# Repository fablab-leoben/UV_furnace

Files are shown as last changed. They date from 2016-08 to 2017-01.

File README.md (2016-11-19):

# UV furnace

## Table of contents

### 1. [Introduction](https://github.com/fablab-leoben/UV_furnace/blob/master/README.md#1-introduction-1 "Introduction")
### 2. [Bill of materials](https://github.com/fablab-leoben/UV_furnace/blob/master/README.md#2-bill-of-materials-1 "Bill of Materials")
### 3. [Required tools](https://github.com/fablab-leoben/UV_furnace/blob/master/README.md#3-required-tools-1 "Required tools")
### 4. [CAD design](https://github.com/fablab-leoben/UV_furnace/blob/master/README.md#4-cad-design-1 "CAD design")
### 5. [Circuit](https://github.com/fablab-leoben/UV_furnace/blob/master/README.md#5-circuit-1 "Circuit")
### 6. [Human Machine Interface (HMI)](https://github.com/fablab-leoben/UV_furnace/blob/master/README.md#6-human-machine-interface-hmi-1 "Human Machine Interface (HMI)")
#### 6.1 [HMI Screenshots](https://github.com/fablab-leoben/UV_furnace/blob/master/README.md#61-hmi-screenshots-1 "HMI Screenshots")
#### 6.2 [Flashing the display](https://github.com/fablab-leoben/UV_furnace/blob/master/README.md#62-flashing-the-display-1 "Flashing the display")
### 7. [Arduino MEGA 2560](https://github.com/fablab-leoben/UV_furnace/blob/master/README.md#7-arduino-mega-2560-1 "Arduino MEGA 2560")
#### 7.1 [Arduino IDE](https://github.com/fablab-leoben/UV_furnace/blob/master/README.md#71-arduino-ide-1 "Arduino IDE")
#### 7.2 [Installing the libraries](https://github.com/fablab-leoben/UV_furnace/blob/master/README.md#72-installing-the-libraries-1 "Installing the libraries")
#### 7.3 [Flashing the code](https://github.com/fablab-leoben/UV_furnace/blob/master/README.md#73-flashing-the-code-1 "Flashing the code")
### 8. [App](https://github.com/fablab-leoben/UV_furnace/blob/master/README.md#8-app-1 "App")
#### 8.1 [Screenshot](https://github.com/fablab-leoben/UV_furnace/blob/master/README.md#81-screenshot-1 "Screenshot")
#### 8.2 [Measuring the temperature](https://github.com/fablab-leoben/UV_furnace/blob/master/README.md#82-measuring-the-temperature-1 "Measuring the temperature")
#### 8.3 [Time and alarms](https://github.com/fablab-leoben/UV_furnace/blob/master/README.md#83-time-and-alarms-1 "Time and alarms")
#### 8.4 [Relay](https://github.com/fablab-leoben/UV_furnace/blob/master/README.md#84-relay-1 "Relay")
#### 8.5 [LEDs](https://github.com/fablab-leoben/UV_furnace/blob/master/README.md#85-leds-1 "LEDs")
#### 8.6 [Persistant data](https://github.com/fablab-leoben/UV_furnace/blob/master/README.md#86-persistant-data-1 "Persistant data")
### 9. [Logging and visualization](https://github.com/fablab-leoben/UV_furnace/blob/master/README.md#9-logging-and-visualization-1 "Logging and visualization")
#### 9.1 [Requirements](https://github.com/fablab-leoben/UV_furnace/blob/master/README.md#91-requirements-1 "Requirements")
#### 9.2 [Install InfluxDB & Grafana](https://github.com/fablab-leoben/UV_furnace/blob/master/README.md#92-install-influxdb--grafana-1 "Install InfluxDB & Grafana")
#### 9.3 [Configuration](https://github.com/fablab-leoben/UV_furnace/blob/master/README.md#93-configuration-1 "Configuration")
##### 9.3.1 [InfluxDB](https://github.com/fablab-leoben/UV_furnace/blob/master/README.md#931-influxdb "InfluxDB")
##### 9.3.2 [Grafana](https://github.com/fablab-leoben/UV_furnace/blob/master/README.md#932-grafana "Grafana")
#### 9.4 [Demonstration](https://github.com/fablab-leoben/UV_furnace/blob/master/README.md#94-demonstration-1 "Demonstration")
### 10. [App](https://github.com/fablab-leoben/UV_furnace/blob/master/README.md#10-app-1 "App")
#### 10.1 [Features](https://github.com/fablab-leoben/UV_furnace/blob/master/README.md#101-features "Features")
#### 10.2 [App installation](https://github.com/fablab-leoben/UV_furnace/blob/master/README.md#101-app-installation-1 "App installation")
### 11. [To Do](https://github.com/fablab-leoben/UV_furnace/blob/master/README.md#11-to-do-1 "To Do")

### 1. Introduction

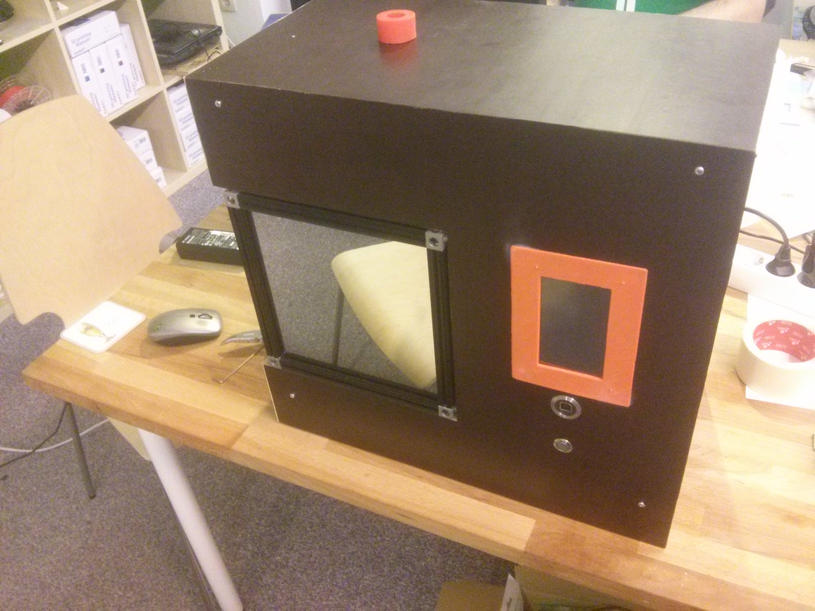
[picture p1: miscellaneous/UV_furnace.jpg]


3D printing is an advanced and environmentally friendly manufacturing method. It is a rapidly growing market both private and commercial. It is not just that they help you to act out your creativity or building prototypes, you are also able to repair things where you will not get any spare parts. They are also used in the medical and aerospace industry!
[SLA](https://en.wikipedia.org/wiki/Selective_laser_sintering) and [DLP](https://en.wikipedia.org/wiki/Digital_Light_Processing) printer are growing increasingly from an expensive niche to a consumer product.
The [Fablab in Leoben](http://www.fablab-leoben.at/) has a commercial [Form One](http://formlabs.com/de/produkte/3d-printers/form-1-plus/) and a **self built** [DLP printer](https://github.com/fablab-leoben/Fab-dlp). These printers usually need some form of post curing with additional UV light and heat to strengthen the printed parts. This would help to open more application areas for SLA/DLP resin printer to help saving ressources and our environment.
During our DLP printer build and because of our experience with the Form One we tried several methods to post-cure the parts after printing. The perfect solution was not found in our experiments so we decided to build our own UV furnace.

Broken parts printed with a Formlabs Form One SLA printer:
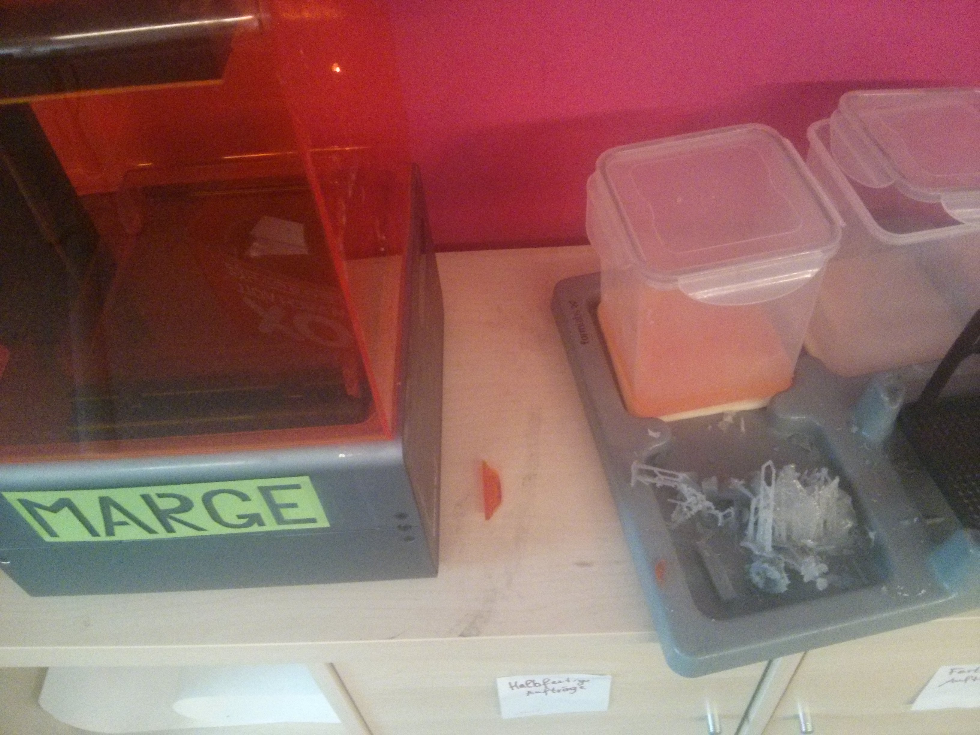
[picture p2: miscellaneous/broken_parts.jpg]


DLP Printer of the Fablab Leoben:
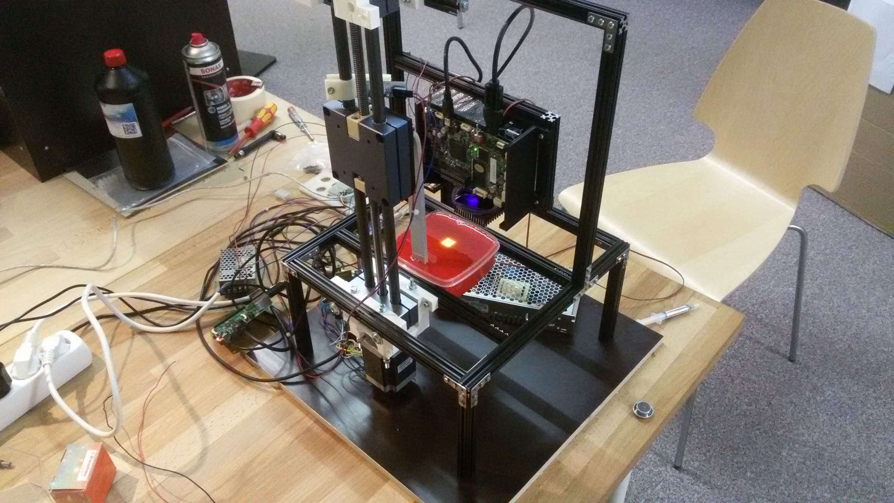
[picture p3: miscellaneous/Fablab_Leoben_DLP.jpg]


Successfull print of [Aria the Dragon](https://www.youmagine.com/designs/aria-the-dragon)
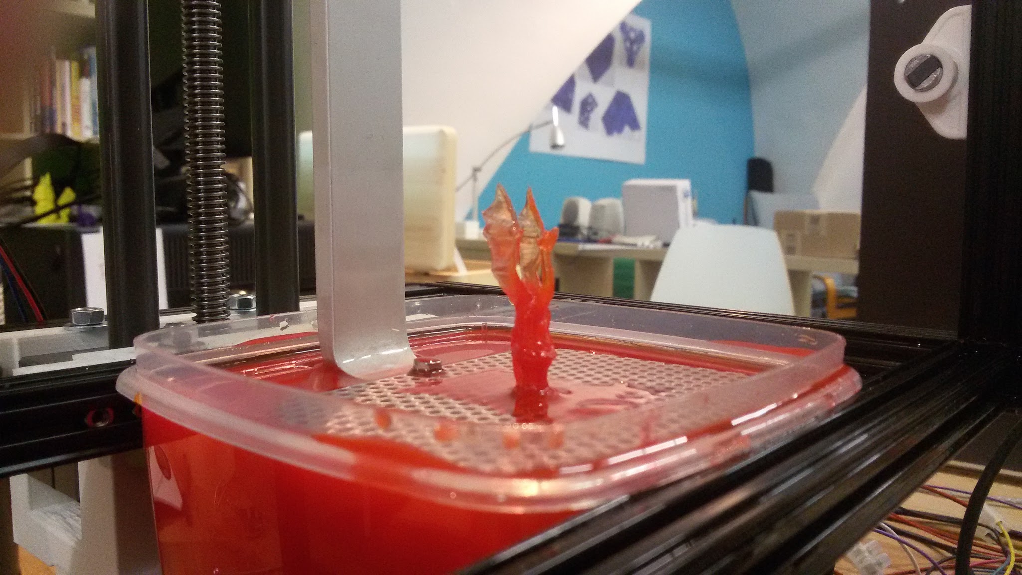
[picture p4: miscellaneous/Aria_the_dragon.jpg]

It looks great but you have to be very careful because the resin is not fully cured. So it is an ideal candidate for the UV furnace.

During the last few months I have designed and built this furnace. It is already working but still under heavy development to include new features and fix small bugs. 

UV furnace video (http://www.youtube.com/watch?v=noe39QOHljc)

### 2. Bill of materials

| Pos. | Pieces | Unit |  Name | comment |
|---|---|---|---|---|
| 1  | 1 |  []  | Arduino Mega 2560 R3 | |
| 2  | 1 |  []  | Arduino Ethernet Shield 2 | |
| 3  | 1 |  []  | Adafruit Thermoelement-Verstärker MAX31855 breakout board - v2.0 | |
| 4  | 1 |  []  | Thermocouple Type-K Glass Braid Insulated - K | |
| 5  | 1 |  []  | Adafruit Magnetic contact switch (door sensor) | Normally open reed switch |
| 6  | 2 |  []  | Kingston 8 GB Micro-SDHC Class10 Speicherkarte | any Micro-SD card is ok |
| 7  | 1 |  []  | Adafruit ChronoDot - Ultra-precise Real Time Clock - v2.1 | |
| 8  | 1 |  []  | Adafruit VEML6070 UV Index Sensor Breakout | optional |
| 9  | 1 |  []  | Adafruit Rugged Metal Pushbutton with LED Ring | |
|  10  | 1 |  []  | Male DC Power adapter - 2.1mm plug to screw terminal block | |
|  11  | 1 |  []  | 5V 1 channel relay shield for Arduino | |
|  12  | 1 |  []  | MEAN WELL RS-25-12 | |
|  13  | 1 |  []  | MEAN WELL LDD-350HW | |
|  14  | 2 |  []  | MEAN WELL LDD-500HW | |
|  15  | 3 |  []  | FISCHER ELEKTRONIK SK57750SA | |
|  16  | 1 |  []  | MEAN WELL PM-10-5 | |
|  17  | 1 |  []  | 240 V 50 W heater mat | |
|  18  | 1 |  []  | Nichia SMD LED UV NCSU275 365 nm | on a 10 x 10 mm pcb |
|  19  | 1 |  []  | Nichia SMD LED UV NCSU275 400 nm | on a 10 x 10 mm pcb |
|  20  | 1 |  []  | NIKKISIO 300 nm LED from EQ Photonics GmbH | ~ 260 €/piece (optional)  |
|  21  | 1 |  []  | Arctic Silver Wärmeleitkleber (2x 3.5g) | |
|  22  | 1 |  []  | fused quarz glass plate 200 x 200 x 2 mm | |
|  23  | 1 |  []  | Aluminium plate 200x200x3 | |
|  24  | 1 |  []  | Geocel Plumba Flue Silikondichtmasse, bis+315°C, Kartusche, 310ml | optional |
|  25  | 1 |  []  | IEC-Steckverbinder C14, Tafelmontage, gerade 10A 250 V ac | |
|  26  |  24 |  []  | Openbeam Corner Cubes | |
|  27  |  10 | [m]  | Openbeam beam | |
|  28  |  36 |  []  | Makerbeam Corner brackets | |
|  29  | 4 |  []  | Feet for Openbeam | |
|  30  | 1 |  []  | Thread forming screw set for OpenBeam | |
|  31  |  24 |  []  | MakerBeam Right angle brackets | |
|  32  |  12 |  []  | MakerBeam T brackets | |
|  33  | 2 |  []  | MakerBeam Button Head Socket Bolt | |
|  34  | 1 |  []  | MakerBeam M3 regular nuts | |
|  35  | 1 |  []  | MakerBeam M3 knurled nuts | |
|  36  | 1 |  []  | MakerBeam M3 cap nuts | |
|  37  | 1 |  []  | USB 2.0 Anschlusskabel USB 2.0 Stecker A - USB 2.0 Stecker B 1.80 m | |
|  38  | 1 |  []  | USB 2.0 Anschlusskabel USB 2.0 Stecker A - USB 2.0 Stecker B 0.50 m | |
|  39  | 1 |  []  | USB-Einbaubuchse vorne USB-Buchse Typ B · hinten USB-Buchse Typ A | optional |
|  40  | 1 |  []  | RJ45-Einbaubuchse Buchse, Einbau, Stecker, gerade Pole: 8P8C RRJVA_RJ45 | optional |
|  41  | 1 |  []  | Netzkabel, C13 auf Stecker mit Schutzleiterkontakt, 2,5m, 16 A, 250 V | |
|  42  | 5 |  []  | mirror flagstone 200 x 200 mm | metallised with Aluminium |
|  43  | 1 |  []  | Nextion 4,3" Touch Display NX4827T043 | |
|  44  | 1 |  []  | [Arduino Mega Screw Shield](http://www.crossroadsfencing.com/BobuinoRev17/)| optional |
|  45  | 2 |  []  | Fan SUNON PF80321B1-000U-S99 | optional |
|  46  | 3 |  []  | Resistor 4,7 kOhm | |
|  47  | 1 |  []  | shrink tubing | |
|  48  | 1 |  []  | bell wire or other wires in different colors | |
|  49  | 2 |  []  | small hinge from your local DIY market | |
|  50  | 1 | [m]  | three-pole electric cable 1,5 mm² | |
|  51  | 5 | [m]  | eight-pole bell wire | or other wires with different colors |
|  52  | 1 |  []  | Female/Male 'Extension' Jumper Wires - 40 x 6" | to wire the sensors |
|  53  | 1,5  | [m²] | plywood 12x1000x1500 mm | |

Estimated costs: **~1000 €**

It really depends on your manufacturing possibilities and the shops where you buy the components. Also be aware that we are using a 300 nm UV LED for **~260 €/piece**! Try to recycle parts when you have a low budget and drop expensive nice to have parts like the "USB-Einbaubuchse" and "RJ45-Einbaubuchse" which cost ~40 € each. So there is enough room to cut the costs down :)

### 3. Required tools

| Pos. | Tool | comment |
|---|---|---|
|  1 |  patience ;) | |
|  2 |  different Screwdrivers | |
|  3 |  different hex key drivers | |
|  4 |  3D Printer | |
|  5 |  soldering iron | |
|  6 |  drilling machine | |
|  7 |  different drills | |
|  8 |  hammer | |
|  9 |  small buzzsaw or Lasercutter | |
| 10 |  multimeter | |
| 11 |  jigsaw | |
| 12 |  lighter | for shrink tubing |
| 13 |  [Arduino IDE](https://www.arduino.cc/en/Main/Software)| |
| 14 |  [Nextion Editor](http://nextion.itead.cc/download.html)| to program the display |
| 15 |  Micro SD Card reader | |

### 4. CAD design

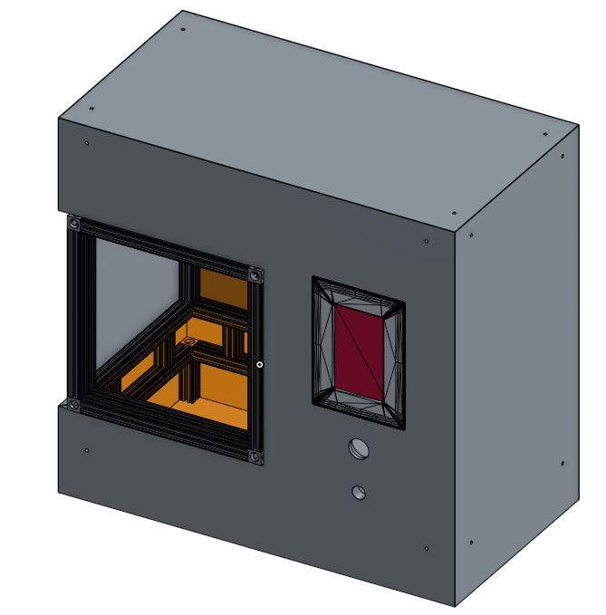
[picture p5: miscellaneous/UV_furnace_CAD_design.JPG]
UV furnace CAD design


The CAD Design was done with [Onshape](https://www.onshape.com/cad-pricing "Onshape"). It is free for Hobbyists, Makers.

You can find, modify and download the UV furnace design [here](https://cad.onshape.com/documents/65acaf65361afb5a9c027038/w/3b13638207107c108fe9135d/e/915e14169c92d702a1d86d80 "UV furnace design"). Feel free to modify the housing to fit your budget. 

### 5. Circuit

I have designed the circuit with [Fritzing](http://fritzing.org/download/). Download the free software to be able to modify the [circuit](https://github.com/fablab-leoben/UV_furnace/blob/master/circuit/UV_furnace_circuit.fzz).
Wire everything like on the picture below and check everything at least twice to make sure everything is wired correctly! Otherwise you can destroy your hardware and jeopardise your health.

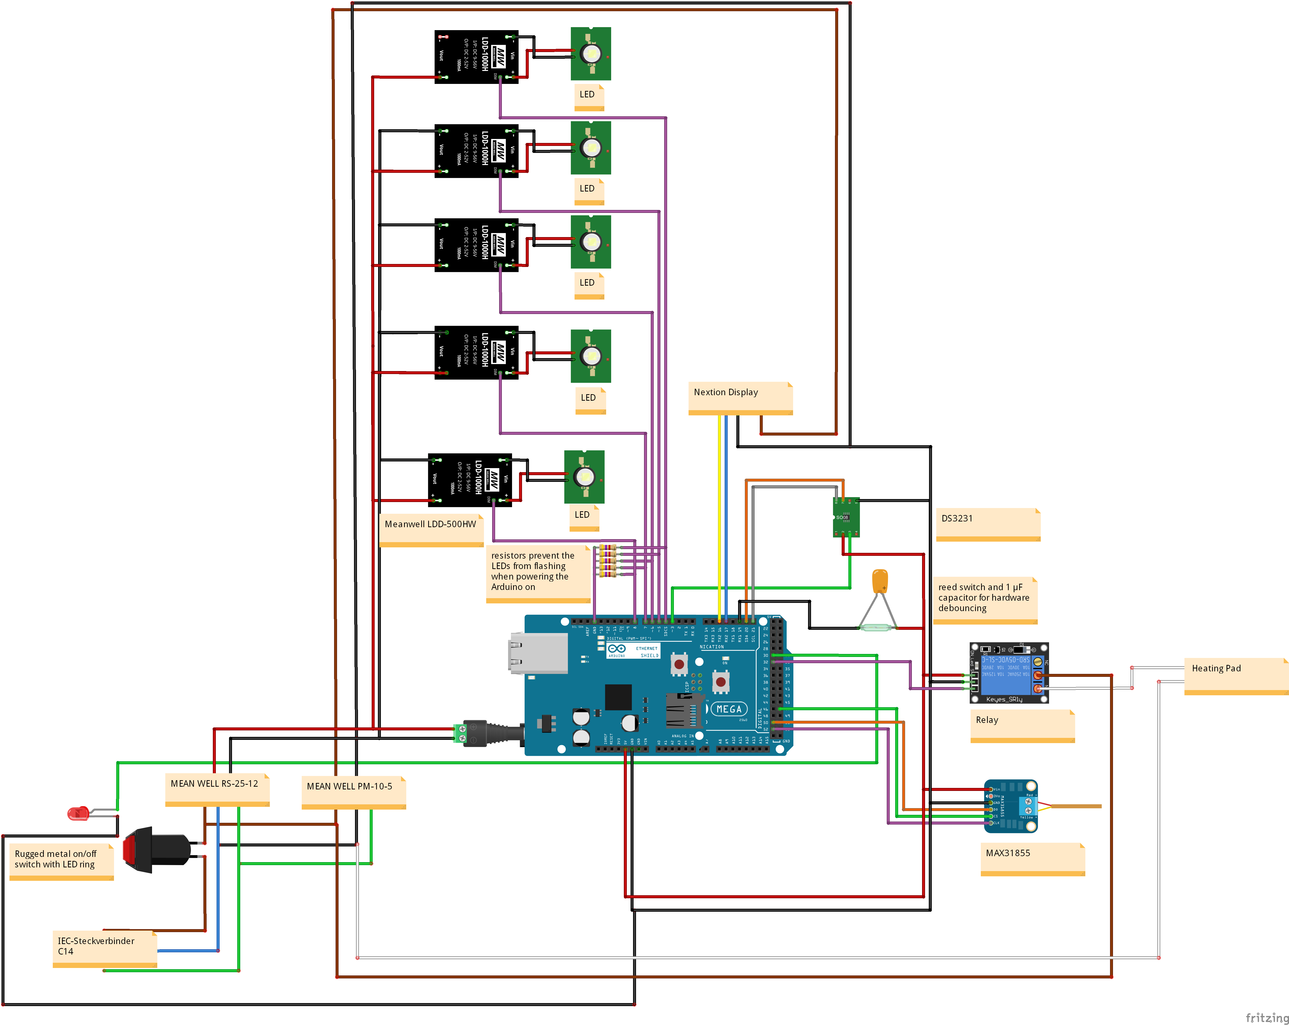
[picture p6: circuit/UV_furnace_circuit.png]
Circuit


Everything mounted in the furnace:
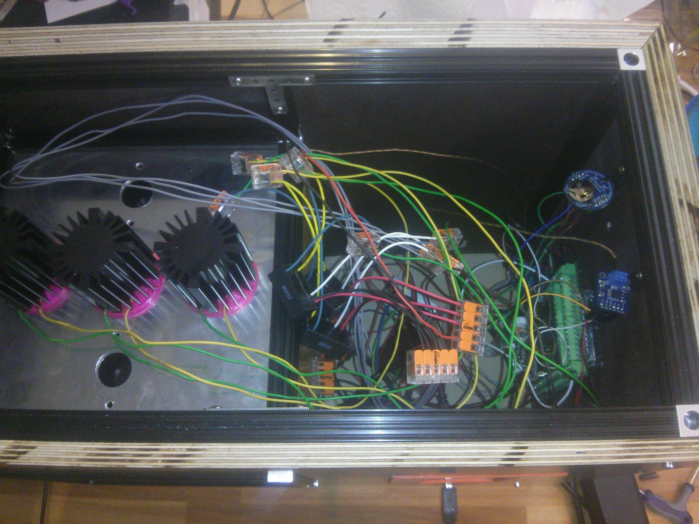
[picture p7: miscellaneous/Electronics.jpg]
Electronics


### 6. Human Machine Interface (HMI)

The HMI was designed with [Pencil](http://pencil.evolus.vn/), an open-source GUI prototyping tool that's available for ALL platforms. The interface is based on the [Material Design Guidelines](https://material.google.com/) from Google for better useability.

#### 6.1 HMI Screenshots

#### 6.2 Flashing the display

Save the [UV_furnace.tft](https://github.com/fablab-leoben/UV_furnace/blob/master/HMI/UV_furnace.tft) file on a micro SD card, insert it into the display and supply it with power. The flash process starts automatically. After that remove the micro SD card and repower the display.
If you would like to make changes to the interface just open [UV_furnace.HMI](https://github.com/fablab-leoben/UV_furnace/blob/master/HMI/UV_furnace.HMI) with the [Nextion editor](http://nextion.itead.cc/download.html).

### 7. Arduino Mega 2560

Because of the comprehensive features I had to use an Arduino Mega for this project.
Visit the [Getting started page](https://www.arduino.cc/en/Guide/HomePage) for more information on how to configure your board.

| Technical specification | |
|---|---|
| Microcontroller |	ATmega2560 |
| Operating Voltage |	5V |
| Input Voltage (recommended) |	7-12V |
| Input Voltage (limit) |	6-20V |
| Digital I/O Pins |	54 (of which 15 provide PWM output) |
| Analog Input Pins |	16 |
| DC Current per I/O Pin |	20 mA |
| DC Current for 3.3V Pin |	50 mA |
| Flash Memory |	256 KB of which 8 KB used by bootloader |
| SRAM	| 8 KB |
| EEPROM	| 4 KB |
| Clock Speed	| 16 MHz |
| Length |	101.52 mm |
| Width |	53.3 mm |
| Weight |	37 g |

#### 7.1 Arduino IDE

First of all download the [Arduino IDE](https://www.arduino.cc/en/Main/Software) and install it on your computer. It is available for Windows, Linux and Mac.

#### 7.2 Installing the libraries

Download the libraries.zip file and extract them into your Arduino libraries folder. The path for Windows computer is: 
>C:\Users\YourName\Documents\Arduino\libraries
If you do not have this folder do not hesitate to create it.

#### 7.3 Flashing the code

Open the Arduino IDE and connect your Arduino via USB to your computer. Under Tools/Board select Arduino Mega and choose the right serial port. 
Open the sketch UV_furnace.ino and click on the compile & flash button. The compiler now translates the code and writes it to your microcontroller.  

### 8. Noteworthy things

#### 8.1. Finite State Machine

My code uses a finite state machine (FSM) to make reading and understanding such a massive amount of code easier for everyone.

Definition of a Finite State Machine:
>A finite-state machine (FSM) or finite-state automaton (FSA, plural: automata), or simply a state machine, is a mathematical model of >computation used to design both computer programs and sequential logic circuits. It is conceived as an abstract machine that can be >in one of a finite number of states. The machine is in only one state at a time; the state it is in at any given time is called the >current state. It can change from one state to another when initiated by a triggering event or condition; this is called a >transition. A particular FSM is defined by a list of its states, and the triggering condition for each transition.

The FSM serves as a manager that organizes the states of the UV furnace.

#### 8.2 Measuring the temperature

The furnace uses a MAX31855 thermocouple amplifier to measure the temperature. You can use thermocouples also for temperatures over 1000 °C. Only the thermocouple is in the hot part of the furnace so you do not need to worry about damaging the amplifier.

#### 8.3 Time and alarms

During startup the furnace requests the current time via the Network Time Protocol (NTP) to set the time of the DS3231 realtime clock. The realtime clock is used to generate an alarm when the furnace has finished. The integrated temperature compensation is also used to check the temperature of the electronics and acts as a safety feature.

#### 8.4 Relay

The UV furnace has a high thermal mass, so the response time is slow. Therefore it is possible to use a cheap relay instead of a solid state relay to control the heating pad. In our case the response time will be 0,1 Hz or once every 10 seconds.
Take care of yourself when you wire the relay because there is mains voltage involved!

#### 8.5 LEDs

I use Meanwell LDD-500H LED driver to control the LEDs. They offer a wide input voltage range from 9 ~ 56 VDC and a high output voltage range from 2 ~ 52 VDC. Hence you are very flexible when you would like to use other LEDs with a different wavelength in your furnace. You only need to change the power supply if necessary. At the moment I am using three LEDs (red, green, white) in the visible light spectrum. Due to the fact that the furnace is under heavy development it is much more comfortable to add features, fix small bugs and test the workflow.
This shows the flexibility of the LED setup. Switching to UV LEDs is only a matter of minutes.

To be able to cure the 3D printed parts the UV light needs to light the curing area. We do not want to stress our light source with unnecessary heat when we cure our prints. Regular glass blocks most of the UV radiation. Because of that we use a quartz glass plate below the LEDs.

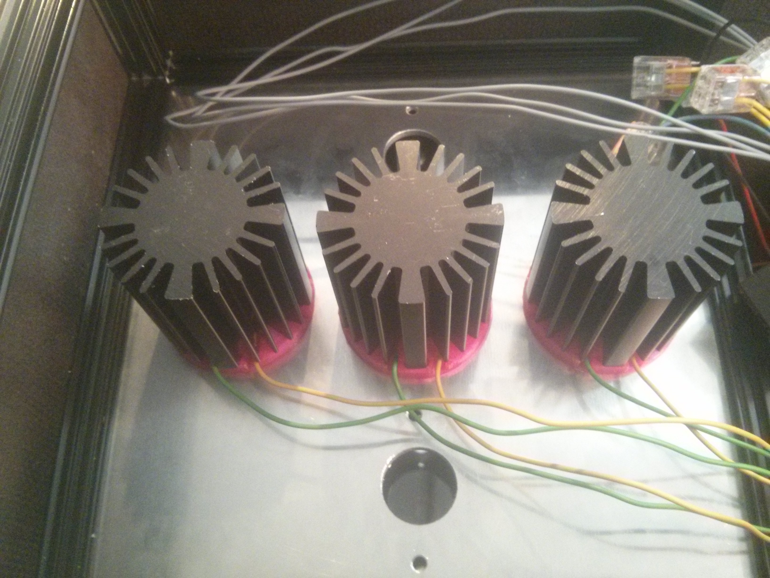
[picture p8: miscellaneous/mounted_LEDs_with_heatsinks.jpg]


#### 8.6 Persistant data

The tuning parameters for the PID controller are saved in the Arduino's EEPROM. Thus the UV furnace will remember the settings from the last time. EEPROM can only be written a finite number of times so we compare the contents before writing.

### 9. Logging and visualization

There are many use cases where data logging and visualization can be very useful so I have made an easy setup to achieve this functionality.

#### 9.1 Requirements
  * Computer running Ubuntu 
  * Install [Docker](docker.com)
  * create directory /media/nas/data/influxdb/
  * create directory /media/nas/data/grafana/
  
#### 9.2 Install InfluxDB & Grafana

Install command for InfluxDB
>sudo docker run -d -p 8083:8083 -p 8086:8086 --name influxdb -p 4444:4444/udp --expose 4444 -e UDP_DB="my_db" -v /media/nas/data/influxdb:/data --restart=unless-stopped tutum/influxdb:0.13

Install command for Grafana
>docker run -d -v /media/nas/data/grafana --name grafana-storage busybox:latest
>docker run -d -p 3000:3000 --name=grafana --volumes-from grafana-storage --restart=unless-stopped grafana/grafana:3.1.1

#### 9.3 Configuration
##### 9.3.1 InfluxDB
In your browser got to yourserver:8083
Change Database to my_db
Under Query Templates create a new user and password for the next step



##### 9.3.2 Grafana

In your browser got to yourserver:3000 and add a new data source:
Name: Influxdb UDP
Type:InfluxDB
URL: yourserveraddress:8086
Access: Proxy
Database: my_db
User and Password you have created in the step before
Save and Test

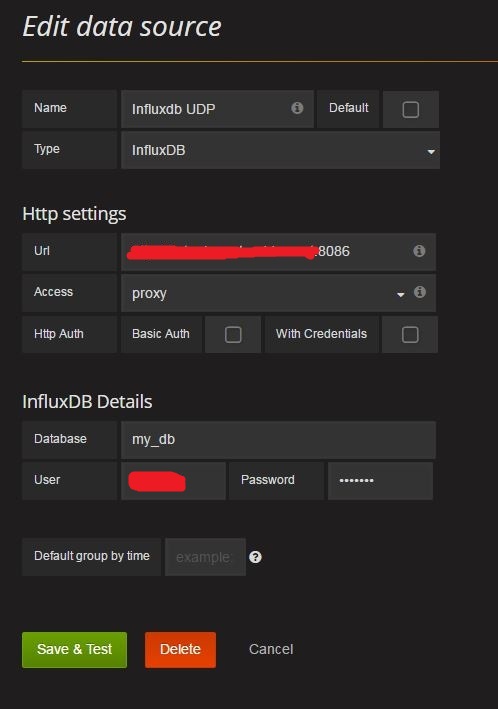
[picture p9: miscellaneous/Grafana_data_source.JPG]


Create a new dashboard:
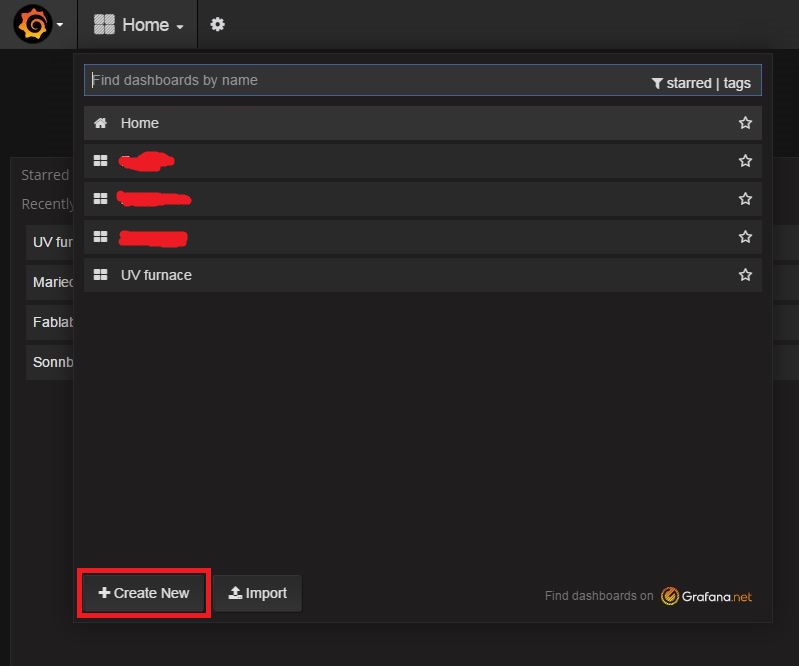
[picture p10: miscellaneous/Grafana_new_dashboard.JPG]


Add a new query:
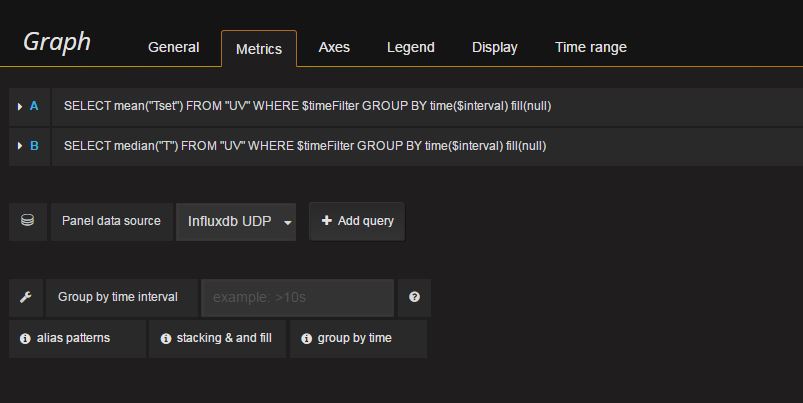
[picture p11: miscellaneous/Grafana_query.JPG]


Save your dashboard and configure the time range in the right corner:
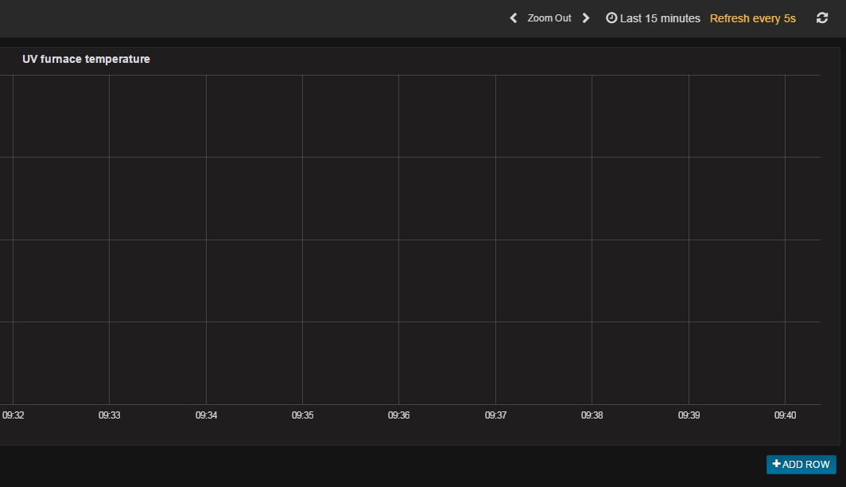
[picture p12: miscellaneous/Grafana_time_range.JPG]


#### 9.4 Demonstration

Start your furnace and you will see the incoming data in your graph:
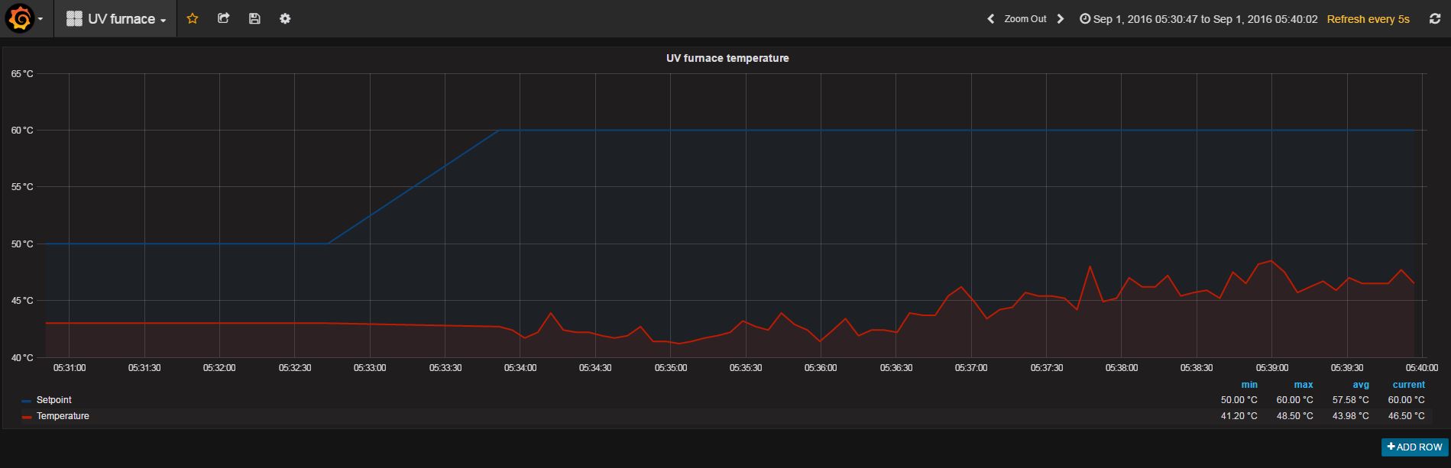
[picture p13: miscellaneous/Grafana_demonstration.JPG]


### 10. App

The smartphone app makes it possible to monitor your furnace when you are not nearby. You will also get a notification when it has finished or if there is an error.

#### 10.1 Features

You can monitor the following things:

* furnace on/off
* LEDs on/off/intensity
* minutes and hours left
* current temperature
* setpoint temperature
* status LED
* temperature chart



The App supports Push, Email and Twitter notifications to inform the User when curing has finished or an error happened.



#### 10.2 App installation

Download and install the Blynk app for your [Android](https://play.google.com/store/apps/details?id=cc.blynk) or [iOS](https://itunes.apple.com/at/app/blynk-iot-for-arduino-raspberry/id808760481?mt=8) device. Now scan the QR code below and replace Auth code in the access.h file. Currently you can see the the setpoint and current temperature. You will get a notification when the furnace is ready. More features will be added in the future.

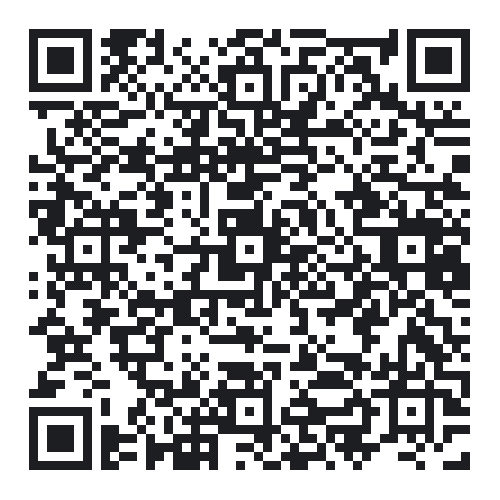
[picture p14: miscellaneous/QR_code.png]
UV furnace App


### 11. To Do

* ~~better display bezel~~
* ~~preheat feature~~
* PID finetuning
* PID tuning without reflashing the sketch
* ~~improving the app~~

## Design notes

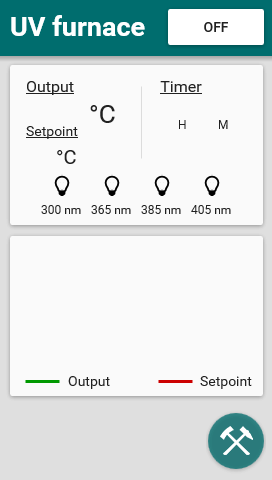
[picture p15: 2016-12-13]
HMI/Overview_OFF.png

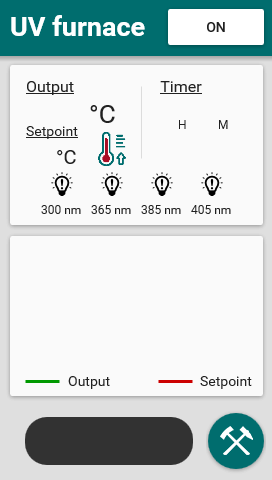
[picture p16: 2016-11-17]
HMI/Overview.png

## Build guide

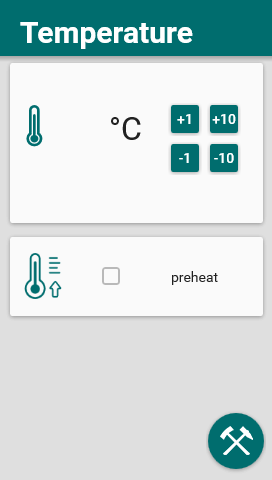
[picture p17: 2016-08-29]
HMI/Temp Setup off.png

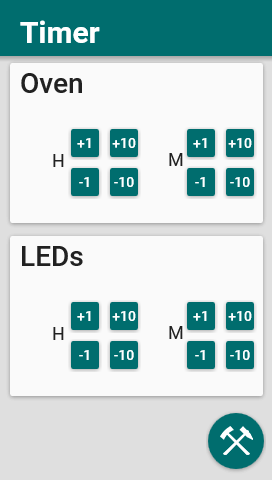
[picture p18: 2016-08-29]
HMI/Timer Setup.png

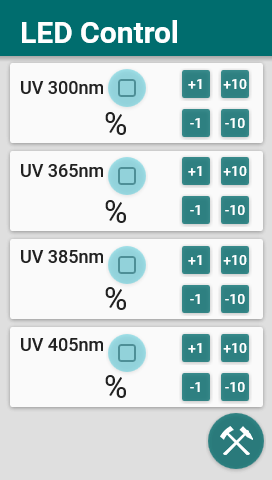
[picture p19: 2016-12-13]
HMI/LED Setup pressed.png

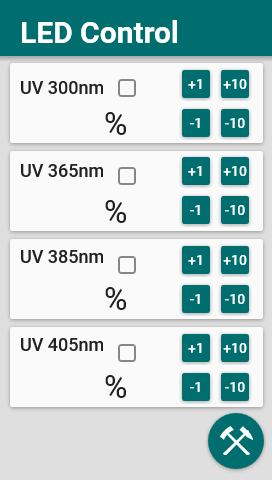
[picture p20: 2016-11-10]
HMI/LED Setup off.png

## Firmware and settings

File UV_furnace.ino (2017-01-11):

/* UV furnace                                                          *
 *                                                                      *
 * Copyright 2016 Thomas Rockenbauer, Fablab Leoben,                    *
 * rockenbauer.thomas@gmail.com                                         *
 *                                                                      *
 * http://www.fablab-leoben.at                                          *
 *                                                                      *
 * http://www.github.com/fablab-leoben                                  *
 *                                                                      *
 * This program is free software; you can redistribute it and/or modify *
 * it under the terms of the GNU General Public License as published by *
 * the Free Software Foundation; either version 2 of the License, or    *
 * (at your option) any later version.                                  *
 *                                                                      *
 * This program is distributed in the hope that it will be useful, but  *
 * WITHOUT ANY WARRANTY; without even the implied warranty of           *
 * MERCHANTABILITY or FITNESS FOR A PARTICULAR PURPOSE. See the GNU     *
 * General Public License for more details.                             *
 *                                                                      *
 * You should have received a copy of the GNU General Public License    *
 * along with this program; if not, write to the Free Software          *
 * Foundation, Inc., 59 Temple Place, Suite 330, Boston,                *
 * MA 02111-1307 USA                                                    *
 *----------------------------------------------------------------------*/

#include <Arduino.h>
#include <Wire.h>
#include <SoftwareSerial.h>
#include <BlynkSimpleEthernet2.h>
#include <Ethernet2.h>
#include <EthernetUdp2.h>
#include "access.h"
#include "configuration.h"
#include <PID_AutoTune_v0.h>
#include <PID_v1.h>
//Library for DS3231 clock
#include <DS3232RTC.h>
//Library for LCD touch screen
#include <Nextion.h>
#include <TimeLib.h>
#include <Timezone.h>
#include <SPI.h>
#include "SD.h"
// So we can save and retrieve settings
#include <EEPROM.h>
#include <Adafruit_MAX31855.h>
#include <elapsedMillis.h>
#include <FiniteStateMachine.h>
#include <SDConfigFile.h>
#include "NexUpload.h"
#include <SoftReset.h>
#include <stdlib.h>

#define APP_NAME "UV furnace"
const char VERSION[] = "0.2";

struct myBoolStruct
{
   uint8_t preset1: 1;
   uint8_t preset2: 1;
   uint8_t preset3: 1;
   uint8_t preset4: 1;
   uint8_t preset5: 1;
   uint8_t preset6: 1;
   uint8_t preheat: 1;

   uint8_t bLED1State: 1;
   uint8_t bLED2State: 1;
   uint8_t bLED3State: 1;
   uint8_t bLED4State: 1;

   uint8_t didReadConfig: 1;
};
myBoolStruct myBoolean;

//compatibility with Arduino IDE 1.6.9
void dummy(){}

/*******************************************************************************
 initialize FSM states with proper enter, update and exit functions
*******************************************************************************/
State dummyState = State(dummy);
State initState = State( initEnterFunction, initUpdateFunction, initExitFunction );
State idleState = State( idleEnterFunction, idleUpdateFunction, idleExitFunction );
State settingsState = State( settingsEnterFunction, settingsUpdateFunction, settingsExitFunction );
State setLEDs = State( setLEDsEnterFunction, setLEDsUpdateFunction, setLEDsExitFunction );
State setTemp = State( setTempEnterFunction, setTempUpdateFunction, setTempExitFunction );
State setTimer = State( setTimerEnterFunction, setTimerUpdateFunction, setTimerExitFunction );
State setPID = State( setPIDEnterFunction, setPIDUpdateFunction, setPIDExitFunction );
State runState = State( runEnterFunction, runUpdateFunction, runExitFunction );
State errorState = State( errorEnterFunction, errorUpdateFunction, errorExitFunction );
State offState = State ( offEnterFunction, offUpdateFunction, offExitFunction );
State preheatState = State ( preheatEnterFunction, preheatUpdateFunction, preheatExitFunction );

//initialize state machine, start in state: Idle
FSM uvFurnaceStateMachine = FSM(initState);

//milliseconds for the init cycle, so everything gets stabilized
#define INIT_TIMEOUT 5000
elapsedMillis initTimer;

/************************************************
 Pin definitions
************************************************/

// LEDs
#define LED1 5
#define LED2 6
#define LED3 7
#define LED4 8
#define LEDlight 9

// Output relay
#define RelayPin 32

// Reed switch
#define reedSwitch 19
volatile boolean doorChanged;

// ON/OFF Button LED
#define onOffButton 12

/************************************************
 LED variables
************************************************/
uint32_t LED1_intensity = 100;
uint32_t LED2_intensity = 100;
uint32_t LED3_intensity = 100;
uint32_t LED4_intensity = 100;

uint32_t LED1_mapped = 0;
uint32_t LED2_mapped = 0;
uint32_t LED3_mapped = 0;
uint32_t LED4_mapped = 0;

/************************************************
Config files
************************************************/
const char CONFIG_preset1[] = "preset1.cfg";
const char CONFIG_preset2[] = "preset2.cfg";
const char CONFIG_preset3[] = "preset3.cfg";
const char CONFIG_preset4[] = "preset4.cfg";
const char CONFIG_preset5[] = "preset5.cfg";
const char CONFIG_preset6[] = "preset6.cfg";

boolean readConfiguration();

/************************************************
Ethernet
************************************************/
#define W5200_CS  10

const unsigned int localPort = 8888;       // local port to listen for UDP packets
char timeServer[] = "time.nist.gov"; // time.nist.gov NTP server
const int NTP_PACKET_SIZE = 48; // NTP time stamp is in the first 48 bytes of the message
byte packetBuffer[NTP_PACKET_SIZE]; //buffer to hold incoming and outgoing packets
bool ethernetAvailable = false;

// A UDP instance to let us send and receive packets over UDP
EthernetUDP Udp;

/************************************************
 PID Variables and constants
************************************************/
//Define Variables we'll be connecting to
double Setpoint;
double Input;
double Output;

volatile unsigned long onTime = 0;

// pid tuning parameters
double Kp;
double Ki;
double Kd;

// EEPROM addresses for persisted data
const int SpAddress = 0;
const int KpAddress = 8;
const int KiAddress = 16;
const int KdAddress = 24;

//Specify the links and initial tuning parameters
PID myPID(&Input, &Output, &Setpoint, Kp, Ki, Kd, DIRECT);

// 10 second Time Proportional Output window
const int WindowSize = 10000;
unsigned long windowStartTime;

/************************************************
 Auto Tune Variables and constants
************************************************/
byte ATuneModeRemember = 2;

double aTuneStep = 500;
double aTuneNoise = 1;
unsigned int aTuneLookBack = 20;

boolean tuning = false;

PID_ATune aTune(&Input, &Output);

/************************************************
 Timer Variables
************************************************/
byte hourAlarm = 0;
byte minuteAlarm = 0;
byte secondAlarm = 0;
uint16_t dayAlarm = 0;

/************************************************
 time settings variables for heating and leds
************************************************/
uint32_t hours_oven = 0;
uint32_t minutes_oven = 0;

uint32_t hours_LED = 0;
uint32_t minutes_LED = 0;

/************************************************
 chart definitions for Nextion 4,3" display
************************************************/
#define inputOffset 0

/*******************************************************************************
 MAX31855 Thermocouple Amplifier
 Creating a thermocouple instance with software SPI on any three
 digital IO pins.
*******************************************************************************/
//#define DO   22
//#define CS   23
//#define CLK  24
#define MAX31855_SAMPLE_INTERVAL   100    // Sample room temperature every 5 seconds
//Adafruit_MAX31855 thermocouple(CLK, CS, DO);
#define cs_MAX31855   47
Adafruit_MAX31855 thermocouple(cs_MAX31855);
elapsedMillis MAX31855SampleInterval;
float currentTemperature;
float lastTemperature;
bool newTemperature = false;

const int NUMBER_OF_SAMPLES = 10;
#define DUMMY -100
#define DUMMY_ARRAY { DUMMY, DUMMY, DUMMY, DUMMY, DUMMY, DUMMY, DUMMY, DUMMY, DUMMY, DUMMY };
float temperatureSamples[NUMBER_OF_SAMPLES] = DUMMY_ARRAY;
float averageTemperature;

/*******************************************************************************
 DS3231
*******************************************************************************/
#define SQW_PIN 3
#define DS3231_TEMP_INTERVAL   2000
elapsedMillis DS3231TempInterval;
time_t t;

//Central European Time (Vienna, Berlin)
TimeChangeRule myCEST = {"CEST", Last, Sat, Mar, 2, +120};    //Daylight time = UTC + 2 hours
TimeChangeRule myCET = {"CET", Sun, Sun, Oct, 3, +60};     //Standard time = UTC + 1 hours
Timezone myTZ(myCEST, myCET);

TimeChangeRule *tcr;        //pointer to the time change rule, use to get TZ abbrev
time_t utc, local;

/*******************************************************************************
 Countdown
*******************************************************************************/
#define COUNTDOWN_UPDATE_INTERVAL   1000
elapsedMillis CountdownUpdateInterval;

/*******************************************************************************
 Power LED
*******************************************************************************/
#define POWERLED_BLINK_INTERVAL   500
elapsedMillis POWERLEDBlinkInterval;
boolean onOffState = HIGH;

unsigned long fadeTime = 0;
byte fadeValue;
int periode = 2000;

/*******************************************************************************
 Graph
*******************************************************************************/
#define GRAPH_UPDATE_INTERVAL   5000
elapsedMillis GraphUpdateInterval;

/*******************************************************************************
 InfluxDB
*******************************************************************************/
#define INFLUXDB_UPDATE_INTERVAL   5000
elapsedMillis InfluxdbUpdateInterval;
char msg[30];

/*******************************************************************************
 Blynk
 Your blynk token goes in another file to avoid sharing it by mistake
*******************************************************************************/
#define BLYNK_INTERVAL   10000
elapsedMillis BlynkInterval;

int pushNotification = 0;
int emailNotification = 0;
int twitterNotification = 0;
#define BLYNK_GREEN     "#23C48E"
#define BLYNK_YELLOW    "#ED9D00"
#define BLYNK_RED       "#D3435C"

/*******************************************************************************
 SD-Card
*******************************************************************************/
const int SDCARD_CS = 4;
File dataFile;
#define SD_CARD_SAMPLE_INTERVAL   1000
elapsedMillis sdCard;

/*******************************************************************************
 Display
*******************************************************************************/

/*******************************************************************************
 interrupt service routine for DS3231 clock
*******************************************************************************/
volatile boolean alarmIsrWasCalled = false;

void alarmIsr(){
    alarmIsrWasCalled = true;
}

/*******************************************************************************
 Nextion 4,3" LCD touch display
 LCD Variables, constants, declaration
*******************************************************************************/
NexPage page0    = NexPage(0, 0, "page0");
NexPage page1    = NexPage(1, 0, "page1");
NexPage page2    = NexPage(2, 0, "page2");
NexPage page3    = NexPage(3, 0, "page3");
NexPage page4    = NexPage(4, 0, "page4");
NexPage page5    = NexPage(5, 0, "page5");
NexPage page6    = NexPage(6, 0, "page6");
NexPage page7    = NexPage(7, 0, "page7");
NexPage page8    = NexPage(8, 0, "page8");
NexPage page9    = NexPage(9, 0, "page9");

/*
 * Declare a button object [page id:0,component id:1, component name: "b0"].
 */

//Page0
NexText tVersion = NexText(0, 1, "tVersion");

//Page1
NexText tTemp = NexText(1, 4, "tTemp");
NexNumber nhour_uv = NexNumber(1, 11, "nhour_uv");
NexNumber nmin_uv = NexNumber(1, 12, "nmin_uv");
NexWaveform sChart = NexWaveform(1, 3, "sChart");
NexButton bSettings = NexButton(1, 1, "bSettings");
NexButton bOnOff = NexButton(1, 2, "bOnOff");
NexNumber nSetpoint = NexNumber(1, 13, "nSetpoint");
NexCrop cLED1 = NexCrop(1, 5, "cLED1");
NexCrop cLED2 = NexCrop(1, 6, "cLED2");
NexCrop cLED3 = NexCrop(1, 7, "cLED3");
NexCrop cLED4 = NexCrop(1, 8, "cLED4");
NexText tToast = NexText(1, 9, "tToast");
NexCrop cPreheat = NexCrop(1, 10, "cPreheat");

//Page2
NexButton bPreSet1   = NexButton(2, 1, "bPreSet1");
NexButton bPreSet2   = NexButton(2, 2, "bPreSet2");
NexButton bPreSet3   = NexButton(2, 3, "bPreSet3");
NexButton bPreSet4   = NexButton(2, 4, "bPreSet4");
NexButton bPreSet5   = NexButton(2, 5, "bPreSet5");
NexButton bPreSet6   = NexButton(2, 6, "bPreSet6");
NexButton bTempSetup   = NexButton(2, 7, "bTempSetup");
NexButton bTimerSetup   = NexButton(2, 8, "bTimerSetup");
NexButton bLEDSetup   = NexButton(2, 9, "bLEDSetup");
NexButton bPIDSetup   = NexButton(2, 10, "bPIDSetup");
NexButton bHomeSet = NexButton(2, 11, "bHomeSet");
NexButton bCredits = NexButton(2, 12, "bCredits");
NexButton bUpdate = NexButton(2, 13, "bUpdate");

//Page3
NexNumber nTempSetup = NexNumber(3, 7, "nTempSetup");
NexButton bHomeTemp = NexButton(3, 5, "bHomeTemp");
NexButton bPreheat = NexButton(3, 6 , "bPreheat");

//Page4
NexButton bHomeTimer = NexButton(4, 17, "bHomeTimer");
NexNumber nOvenHourT = NexNumber(4, 18, "nOvenHourT");
NexNumber nOvenMinuteT = NexNumber(4, 19, "nOvenMinuteT");
NexNumber nLEDsHourT = NexNumber(4, 20, "nLEDsHourT");
NexNumber nLEDsMinuteT = NexNumber(4, 21, "nLEDsMinuteT");
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
void loop() {
  nexLoop(nex_listen_list);
  #ifdef USE_Blynk
    //all the Blynk magic happens here
    Blynk.run();
  #endif
  //this function reads the temperature of the MAX31855 Thermocouple Amplifier

  if(doorChanged == true){
    checkDoor();
    doorChanged = false;
  }

  readTemperature();
  readInternalTemperature();
  updateBlynk();
  if (alarmIsrWasCalled){
     if (RTC.alarm(ALARM_1)) {
        DEBUG_PRINTLN("Alarm_1");
        uvFurnaceStateMachine.transitionTo(offState);
     }
     if (RTC.alarm(ALARM_2)){
        DEBUG_PRINTLN("Alarm_2");
     }
     alarmIsrWasCalled = false;
  }

  //this function updates the FSM
  // the FSM is the heart of the UV furnace - all actions are defined by its states
  uvFurnaceStateMachine.update();
}

/*******************************************************************************
 * Function Name  : checkDoor
 * Description    : updates the value of target temperature of the uv furnace
 * Return         : none
 *******************************************************************************/
void checkDoor(){
  if(digitalRead(reedSwitch) == HIGH){
      digitalWrite(LEDlight, 255);
      controlLEDs(0,0,0,0);
      //DEBUG_PRINTLN("door open");
  }else if(digitalRead(reedSwitch) == LOW){
      if(uvFurnaceStateMachine.isInState(runState)){
        controlLEDs(LED1_intensity, LED2_intensity, LED3_intensity, LED4_intensity);
      }
      digitalWrite(LEDlight, 0);
  }
}

/*******************************************************************************
 * Function Name  : updateTemperature
 * Description    : updates the value of target temperature of the uv furnace
 * Return         : none
 *******************************************************************************/
void updateTemperature()
{
    if(averageTemperature != lastTemperature && newTemperature == true)  {
      dtostrf(averageTemperature, 5, 1, buffer);
      tTemp.setText(buffer);
      lastTemperature = averageTemperature;
    }
    newTemperature = false;
}

/*******************************************************************************
 * Function Name  : readTemperature
 * Description    : reads the temperature of the MAX31855 sensor at every MAX31855_SAMPLE_INTERVAL
                    corrected temperature reading for a K-type thermocouple
                    allowing accurate readings over an extended range
                    http://forums.adafruit.com/viewtopic.php?f=19&t=32086&p=372992#p372992
                    assuming global: Adafruit_MAX31855 thermocouple(CLK, CS, DO);
 * Return         : 0
 *******************************************************************************/
void readTemperature(){
   //time is up? no, then come back later
   if (MAX31855SampleInterval < MAX31855_SAMPLE_INTERVAL) {
    return;
   }

   selMAX31855();

   //time is up, reset timer
   MAX31855SampleInterval = 0;
   // MAX31855 thermocouple voltage reading in mV
   float thermocoupleVoltage = (thermocouple.readCelsius() - thermocouple.readInternal()) * 0.041276;

   // MAX31855 cold junction voltage reading in mV
   float coldJunctionTemperature = thermocouple.readInternal();
   float coldJunctionVoltage = -0.176004136860E-01 +
      0.389212049750E-01  * coldJunctionTemperature +
      0.185587700320E-04  * pow(coldJunctionTemperature, 2.0) +
      -0.994575928740E-07 * pow(coldJunctionTemperature, 3.0) +
      0.318409457190E-09  * pow(coldJunctionTemperature, 4.0) +
      -0.560728448890E-12 * pow(coldJunctionTemperature, 5.0) +
      0.560750590590E-15  * pow(coldJunctionTemperature, 6.0) +
      -0.320207200030E-18 * pow(coldJunctionTemperature, 7.0) +
      0.971511471520E-22  * pow(coldJunctionTemperature, 8.0) +
      -0.121047212750E-25 * pow(coldJunctionTemperature, 9.0) +
      0.118597600000E+00  * exp(-0.118343200000E-03 *
                           pow((coldJunctionTemperature-0.126968600000E+03), 2.0)
                        );

   // cold junction voltage + thermocouple voltage
   float voltageSum = thermocoupleVoltage + coldJunctionVoltage;

   // calculate corrected temperature reading based on coefficients for 3 different ranges
   float b0, b1, b2, b3, b4, b5, b6, b7, b8, b9;
   if(thermocoupleVoltage < 0){
      b0 = 0.0000000E+00;
      b1 = 2.5173462E+01;
      b2 = -1.1662878E+00;
      b3 = -1.0833638E+00;
      b4 = -8.9773540E-01;
      b5 = -3.7342377E-01;
      b6 = -8.6632643E-02;
      b7 = -1.0450598E-02;
      b8 = -5.1920577E-04;
      b9 = 0.0000000E+00;
   }

   else if(thermocoupleVoltage < 20.644){
      b0 = 0.000000E+00;
      b1 = 2.508355E+01;
      b2 = 7.860106E-02;
      b3 = -2.503131E-01;
      b4 = 8.315270E-02;
      b5 = -1.228034E-02;
      b6 = 9.804036E-04;
      b7 = -4.413030E-05;
      b8 = 1.057734E-06;
      b9 = -1.052755E-08;
   }

   else if(thermocoupleVoltage < 54.886){
      b0 = -1.318058E+02;
      b1 = 4.830222E+01;
      b2 = -1.646031E+00;
      b3 = 5.464731E-02;
      b4 = -9.650715E-04;
      b5 = 8.802193E-06;
      b6 = -3.110810E-08;
      b7 = 0.000000E+00;
      b8 = 0.000000E+00;
      b9 = 0.000000E+00;
   }

   else {
      // TODO: handle error - out of range
      return;
   }

   currentTemperature = b0 +
      b1 * voltageSum +
      b2 * pow(voltageSum, 2.0) +
      b3 * pow(voltageSum, 3.0) +
      b4 * pow(voltageSum, 4.0) +
      b5 * pow(voltageSum, 5.0) +
      b6 * pow(voltageSum, 6.0) +
      b7 * pow(voltageSum, 7.0) +
      b8 * pow(voltageSum, 8.0) +
      b9 * pow(voltageSum, 9.0);

    uint8_t i;
    for (i=0; i< NUMBER_OF_SAMPLES; i++) {
        //store the sample in the next available 'slot' in the array of samples
        if ( temperatureSamples[i] == DUMMY) {
            temperatureSamples[i] = currentTemperature;
        break;
        }
    }

    //is the samples array full? if not, exit and get a new sample
    if ( temperatureSamples[NUMBER_OF_SAMPLES-1] == DUMMY) {
        return;
    }

    // average all the samples out
    averageTemperature = 0;

    for (i=0; i<NUMBER_OF_SAMPLES; i++) {
        averageTemperature += temperatureSamples[i];
    }
    averageTemperature /= NUMBER_OF_SAMPLES;
    averageTemperature = int((averageTemperature + 0.05) * 10);
    averageTemperature /= 10;

    //reset samples array to default so we fill it up again with new samples
    for (i=0; i<NUMBER_OF_SAMPLES; i++) {
        temperatureSamples[i] = DUMMY;
    }
    DEBUG_PRINTLN(averageTemperature);
    newTemperature = true;
}

/*******************************************************************************
 * Function Name  : readInternalTemperature
 * Description    : reads the temperature of the DS3231
 * Return         : 0
 *******************************************************************************/
void readInternalTemperature(){
  if(DS3231TempInterval < DS3231_TEMP_INTERVAL) {
    return;
  }

  if(RTC.temperature() / 4.0 > 40) {
    DEBUG_PRINTLN(F("ERROR"));
    uvFurnaceStateMachine.immediateTransitionTo(offState);
  }
}

/*******************************************************************************
 * Function Name  : setDS3231Alarm
 * Description    : sets the alarm for the time the user has choosen
 * Return         : 0
*******************************************************************************/
void setDS3231Alarm(byte minutes, byte hours) {

  //tmElements_t tm;
  //RTC.read(tm);
  t = now();
  DEBUG_PRINTLN(t);
  t += minutes * 60 + hours * 3600;
  DEBUG_PRINTLN(t);
  RTC.setAlarm(ALM1_MATCH_DATE, second(t), minute(t), hour(t), day(t));
  DEBUG_PRINT(hour(t));
  DEBUG_PRINT(":");
  DEBUG_PRINT(minute(t));
  DEBUG_PRINT(":");
  DEBUG_PRINTLN(second(t));
  DEBUG_PRINTLN(day(t));
  RTC.alarm(ALARM_1);
  RTC.alarmInterrupt(ALARM_1, true);

  return;
}
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

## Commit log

2016-06-27 pin definition of max31855
2016-06-27 added time.h, ethernet.h, spi.h, sd.h
2016-06-29 found error for display not reacting
    [UV_furnace.ino]
2016-07-02 added pid and pid autotune library
2016-07-02 added relay pin
2016-07-02 PID Variables and constants
2016-07-02 Initialize the PID and related variables
2016-07-02 Run timer2 interrupt every 15 ms
2016-07-02 Timer2 Overflow Interrupt Enable
2016-07-02 added states run and error
    [UV_furnace.ino]
2016-07-02 switched MAX31855 to hardware spi
2016-07-03 added ntp time synchronisation in setup
    maybe not working as expected
    [UV_furnace.ino]
2016-07-06 reed switch, led button
2016-07-06 changed reed switch pin to 22
2016-07-10 display support for PID autotune
2016-07-11 removed ntp, fixed ethernet
    [UV_furnace.ino]
2016-07-12 check state before updating current temperature
2016-07-13 set pid to automatic before start
2016-07-14 updated LED code
2016-07-14 blinking on/off Button LED
2016-07-17 updated PID code
2016-07-24 fade the power LED
2016-07-24 fix Relay bug
2016-07-24 fix MAX31855 thermocouple bug
    [UV_furnace.ino]
2016-07-24 fix MAX31855 thermocouple bug again
    [UV_furnace.ino]
2016-07-24 read the temperature of the DS3231
2016-07-26 Revert "changed MAC"
    This reverts commit 41b3c27a72060966fb13e82fbb90599b8489226d.
    [UV_furnace.ino]
2016-07-26 removed logging to SD, added config file support, fixed time library
    [UV_furnace.ino]
2016-07-27 support for reading a config file, not tested
    [preset1.cfg]
2016-07-30 cad update
2016-07-31 added circuit
    [Circuit.fzz]
2016-07-31 updated circuit
    [Circuit.fzz, UV_furnace_circuit.fzz]
2016-07-31 updated folder structure
    [UV_furnace_circuit.fzz]
2016-08-01 added credits and error page, removed old pictures
    [UV_furnace.ino]
2016-08-02 fixed display showing wrong pictures
    [UV_furnace.ino]
2016-08-02 fixed minor 2 bugs
    [UV_furnace.ino]
2016-08-03 implement reed switch and DS3231 interrupts
2016-08-05 fix furnace not shutting off
    [UV_furnace.ino]
2016-08-07 update reed switch code
2016-09-01 alarm interrupt working
2016-09-01 InfluxDB logging
    [UV_furnace_circuit.fzz]
2016-09-01 Revert "InfluxDB logging"
    This reverts commit 7500e02ce8b1f67a172437fdc770bee810917fa8.
    [UV_furnace_circuit.fzz]
2016-09-03 many improvements to influxdb, debugging, temperature and bug fixes
    [configuration.h]
2016-09-05 improved blynk integration
    [configuration.h]
2016-09-08 fix Blynk and reed switch
    [UV_furnace.ino]
2016-09-10 added LED light when furnace is open
2016-09-11 blynk update, bug fixes
    [UV_furnace.ino]
2016-11-13 round temperature
2016-11-18 fix rtc
    [configuration.h]
2016-11-20 fix led bug and simplify led code
    [UV_furnace.ino]
2016-11-20 included reset after display update
    [UV_furnace.ino]
2016-11-23 chose between static or dynamic ip
    [configuration.h]
2016-12-07 small fixes
    [configuration.h]
2016-12-10 pid update
2016-12-14 added pid autotune
2016-12-16 maybe fix timer for long curing durations
    [UV_furnace.ino]
